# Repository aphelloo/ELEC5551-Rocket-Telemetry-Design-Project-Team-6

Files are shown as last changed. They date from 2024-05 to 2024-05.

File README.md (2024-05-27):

# ELEC5551-Rocket-Telemetry-Design-Project-Team-6
The purpose of this final design report is to present a TTS design for the UWAAL sub-orbital launch project. The design primarily aims to track the rocket’s sub-orbital launch to 4 km altitude, monitor its descent, identify the landing location for recovery efforts whilst also collect data throughout the entire mission. This is achieved through the development of two modules: one fitting within the designated section of the CubeSat onboard the rocket (i.e. the payload module) that collects & transmits data, and a base station on the ground responsible for collecting information from the payload module and displaying location of the payload module on a user interface akin to Google Maps functionality. The final design will be composed of a hardware and software solution that will address the inclusions stated in this section.

## Authors
* Shraddha Domdala 
* Sharla Greyvenstein 
* Kate Miller 
* Ankona Pahari
* Anusree Rejukumar
* Thomas Robertson

## Repository Structure
* 3D CAD Design: For Base Station Box and Battery Holder (payload module)
* Code: Includes pseudocode and code-flow diagrams
* Construction and Risks: Documentation on construction procedures and risk assessments associated with the project.
* Libraries: Libraries required for KiCAD to open schematics and PCB Layout
* PCB Layout: PCB Layout for base station and payload module
* Schematics: Schematics for base station and payload module
* Simulations: Simulations to test various aspects of the project

## Required Applications
* KiCAD V6 or Later
* MATLAB 2024a

## Library Installation Guide
Under Libraries
Using the *.kicad_sym file:

* Extract the content of the downloaded *.zip file.
* In KiCad, go to Preferences.
* Click on Manage Symbol Libraries.
* On the Global Libraries tab, click on Browse Libraries (the small folder icon)
* Select the .kicad_sym file, then click Open.
* The library will appear, click OK.
* Click on Symbol Editor.
* Type on the filter search field, and navigate to the symbol you imported.
* Double-click over it to open the file.

Using the *.kicad_mod file:

* Extract the content of the downloaded *.zip file.
* In KiCad, go to Preferences.
* Click on Manage Footprint Libraries.
* On the Global Libraries tab, click on Browse Libraries (the small folder icon)
* Navigate to the Folder where the .kicad_mod file is located. Then click Select Folder. (Note: You will not normally see the .kicad_mod file on this step because
  you need to select the folder where it is located.)
* The library will appear, click OK.
* Click on Footprint Editor.
* Type on the filter search field, and navigate to the footprint you imported.
* Double-click over it to open the file.

## Simulation File Installation Guide 
Files are under simulations > spice simulations
* Extract the content of the downloaded *.zip file.
* Go to the voltage regulator and right click on properties
* Then click on Simulation Model
* Click folder near the file tab
* Go to location of LM1117_N_ADJ_TRANS.LIB or TPS7A0530P_TRANS.lib depending on the file (see name of component to see which is right) - do not change anything else in that tab
* Ensure pin assignments for symbol and model pin match each other in the Simulation Model
* Click Ok in Simulation Model
* Click Ok in Properties Tab

## Acknowledgements
Would like to acknowledge the stakeholders of this project for their assistance

## Licence
This project is licensed under the CERN-OHL-P-2.0 license

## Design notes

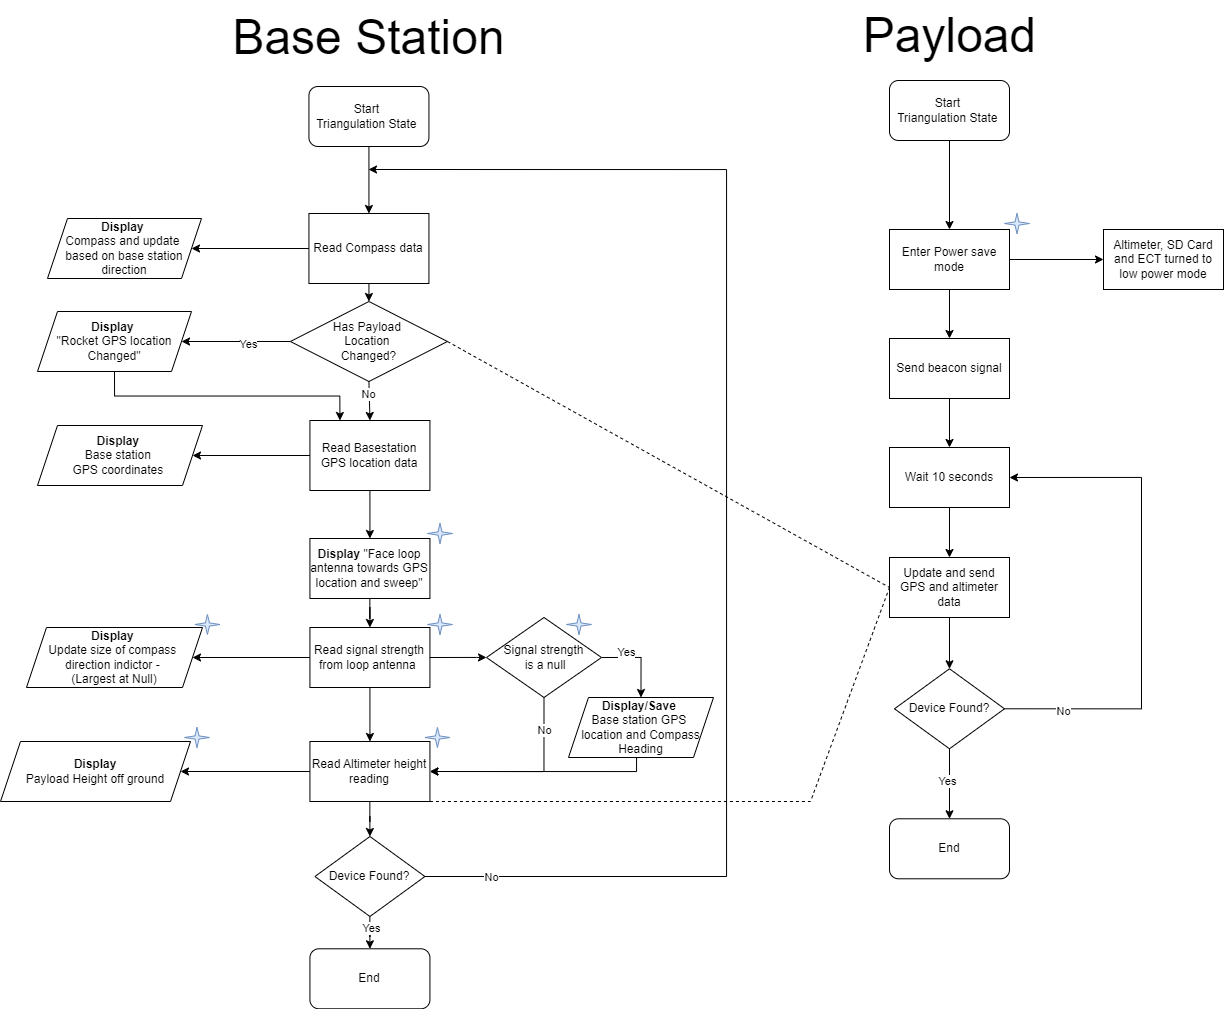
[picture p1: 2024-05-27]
Code/Code Flow/Triangulation Code Flow.png

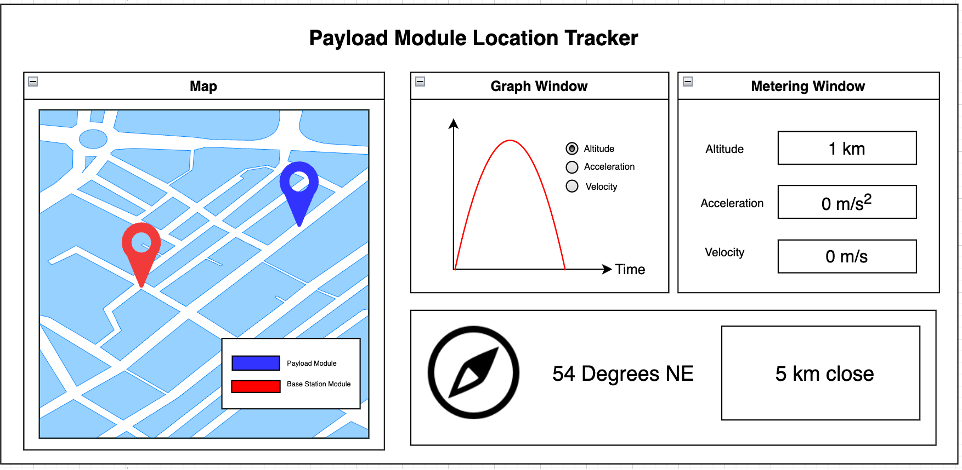
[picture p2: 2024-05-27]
Code/Pseudocode/User Interface Laptop.png

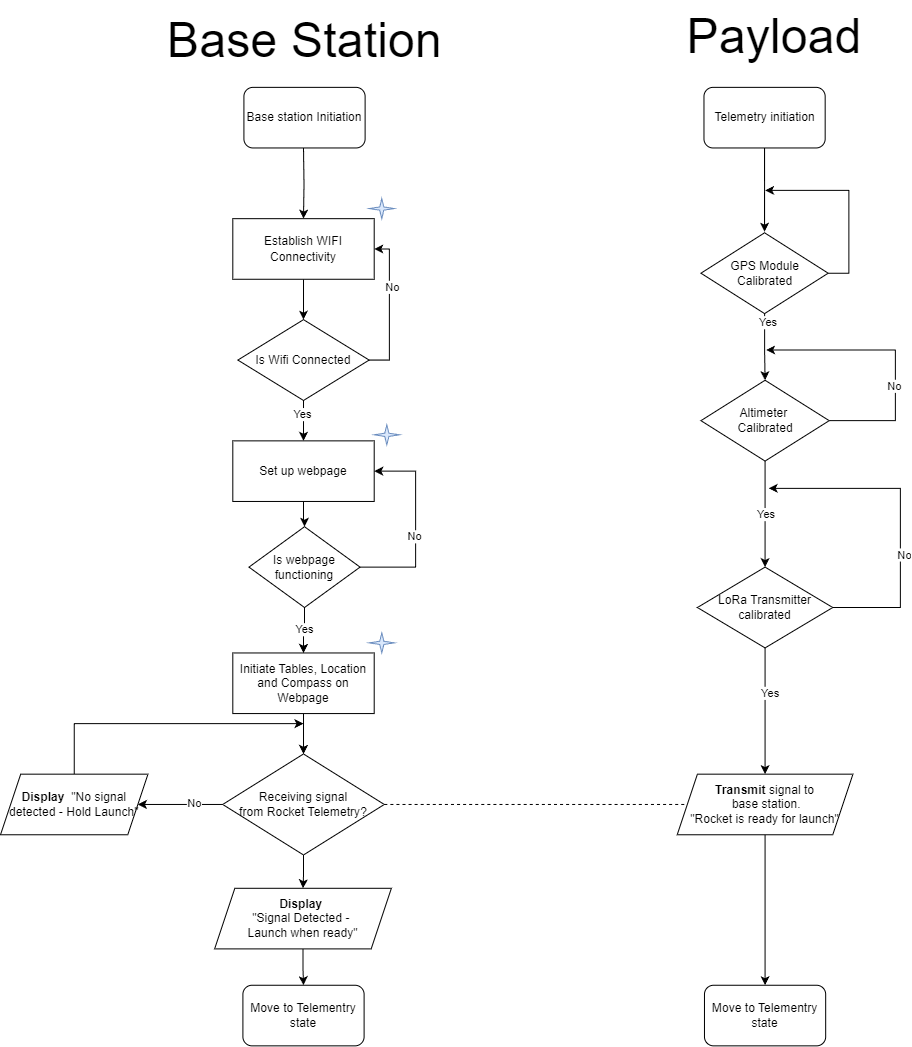
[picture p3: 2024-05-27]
Code/Code Flow/Initiation Code Flow.png

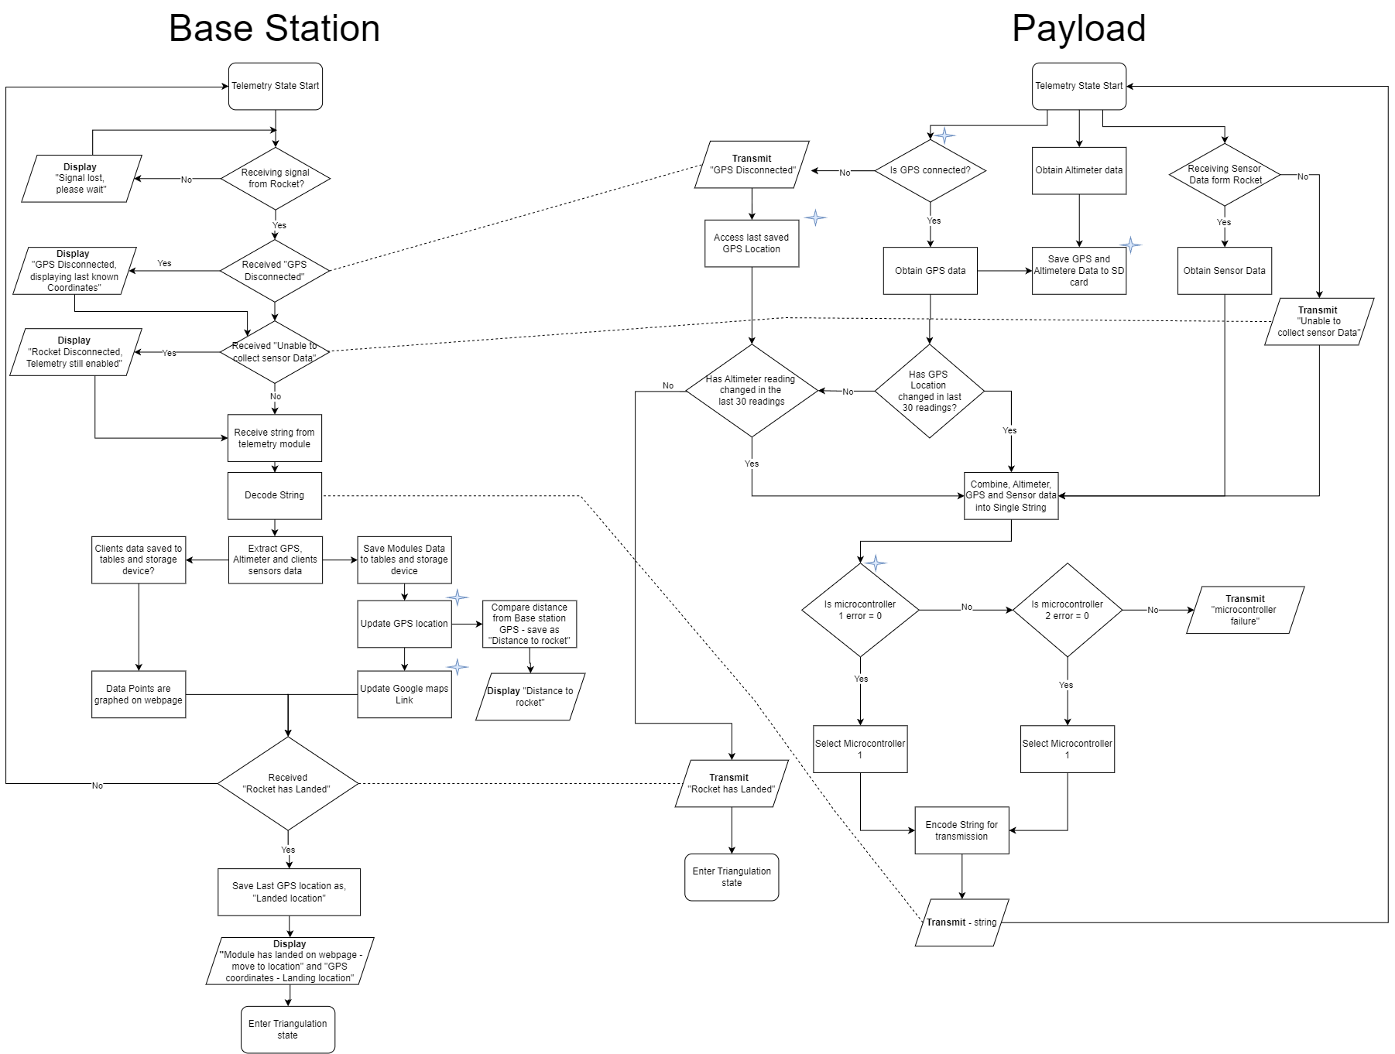
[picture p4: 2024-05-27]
Code/Code Flow/Telementry Code Flow.png

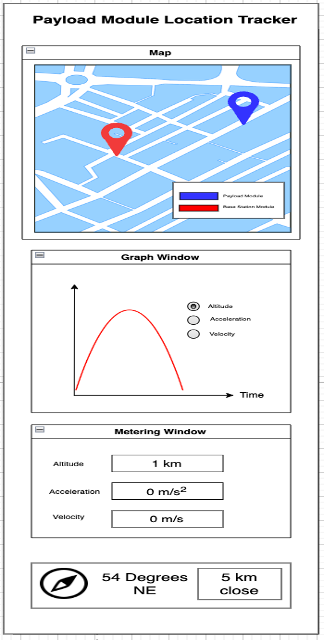
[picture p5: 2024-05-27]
Code/Pseudocode/User Interface Phone.png

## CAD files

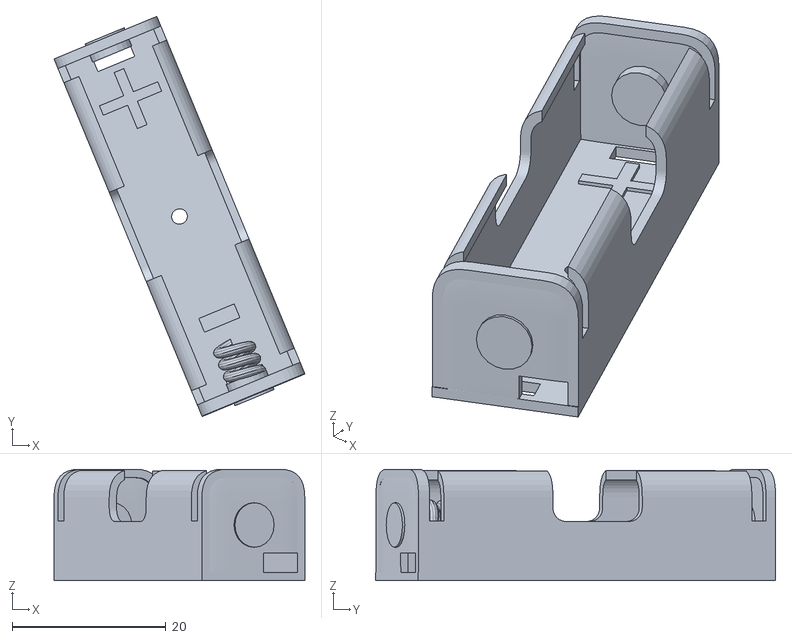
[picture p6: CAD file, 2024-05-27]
3D CAD Design/Team 6 Complete Battery Holder with Contacts and Springs.stl
32.7 x 52.1 x 14.5

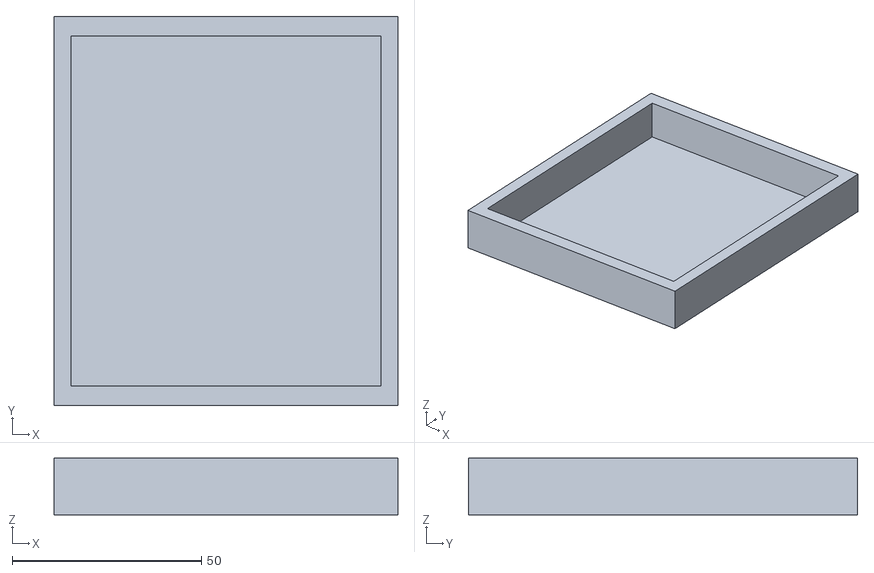
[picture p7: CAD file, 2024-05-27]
3D CAD Design/Team 6 Base Station Bottom.stl
91.0 x 103.0 x 15.0

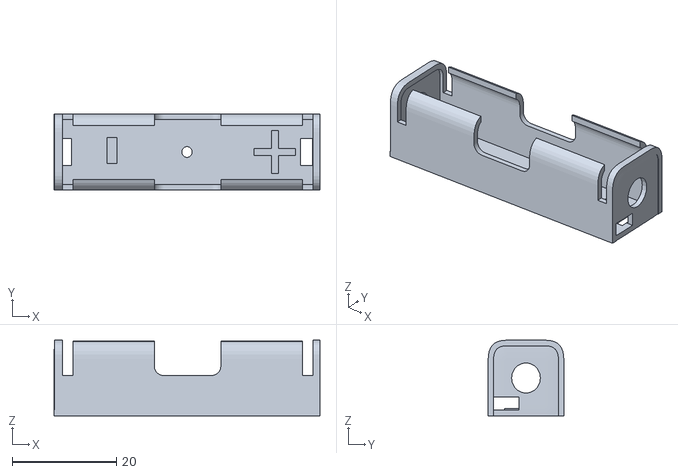
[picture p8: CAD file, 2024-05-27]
3D CAD Design/Team 6 Battery Holder without Contacts.stl
51.0 x 14.5 x 14.5

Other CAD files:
3D CAD Design/Team 6 Base Station Top.stl

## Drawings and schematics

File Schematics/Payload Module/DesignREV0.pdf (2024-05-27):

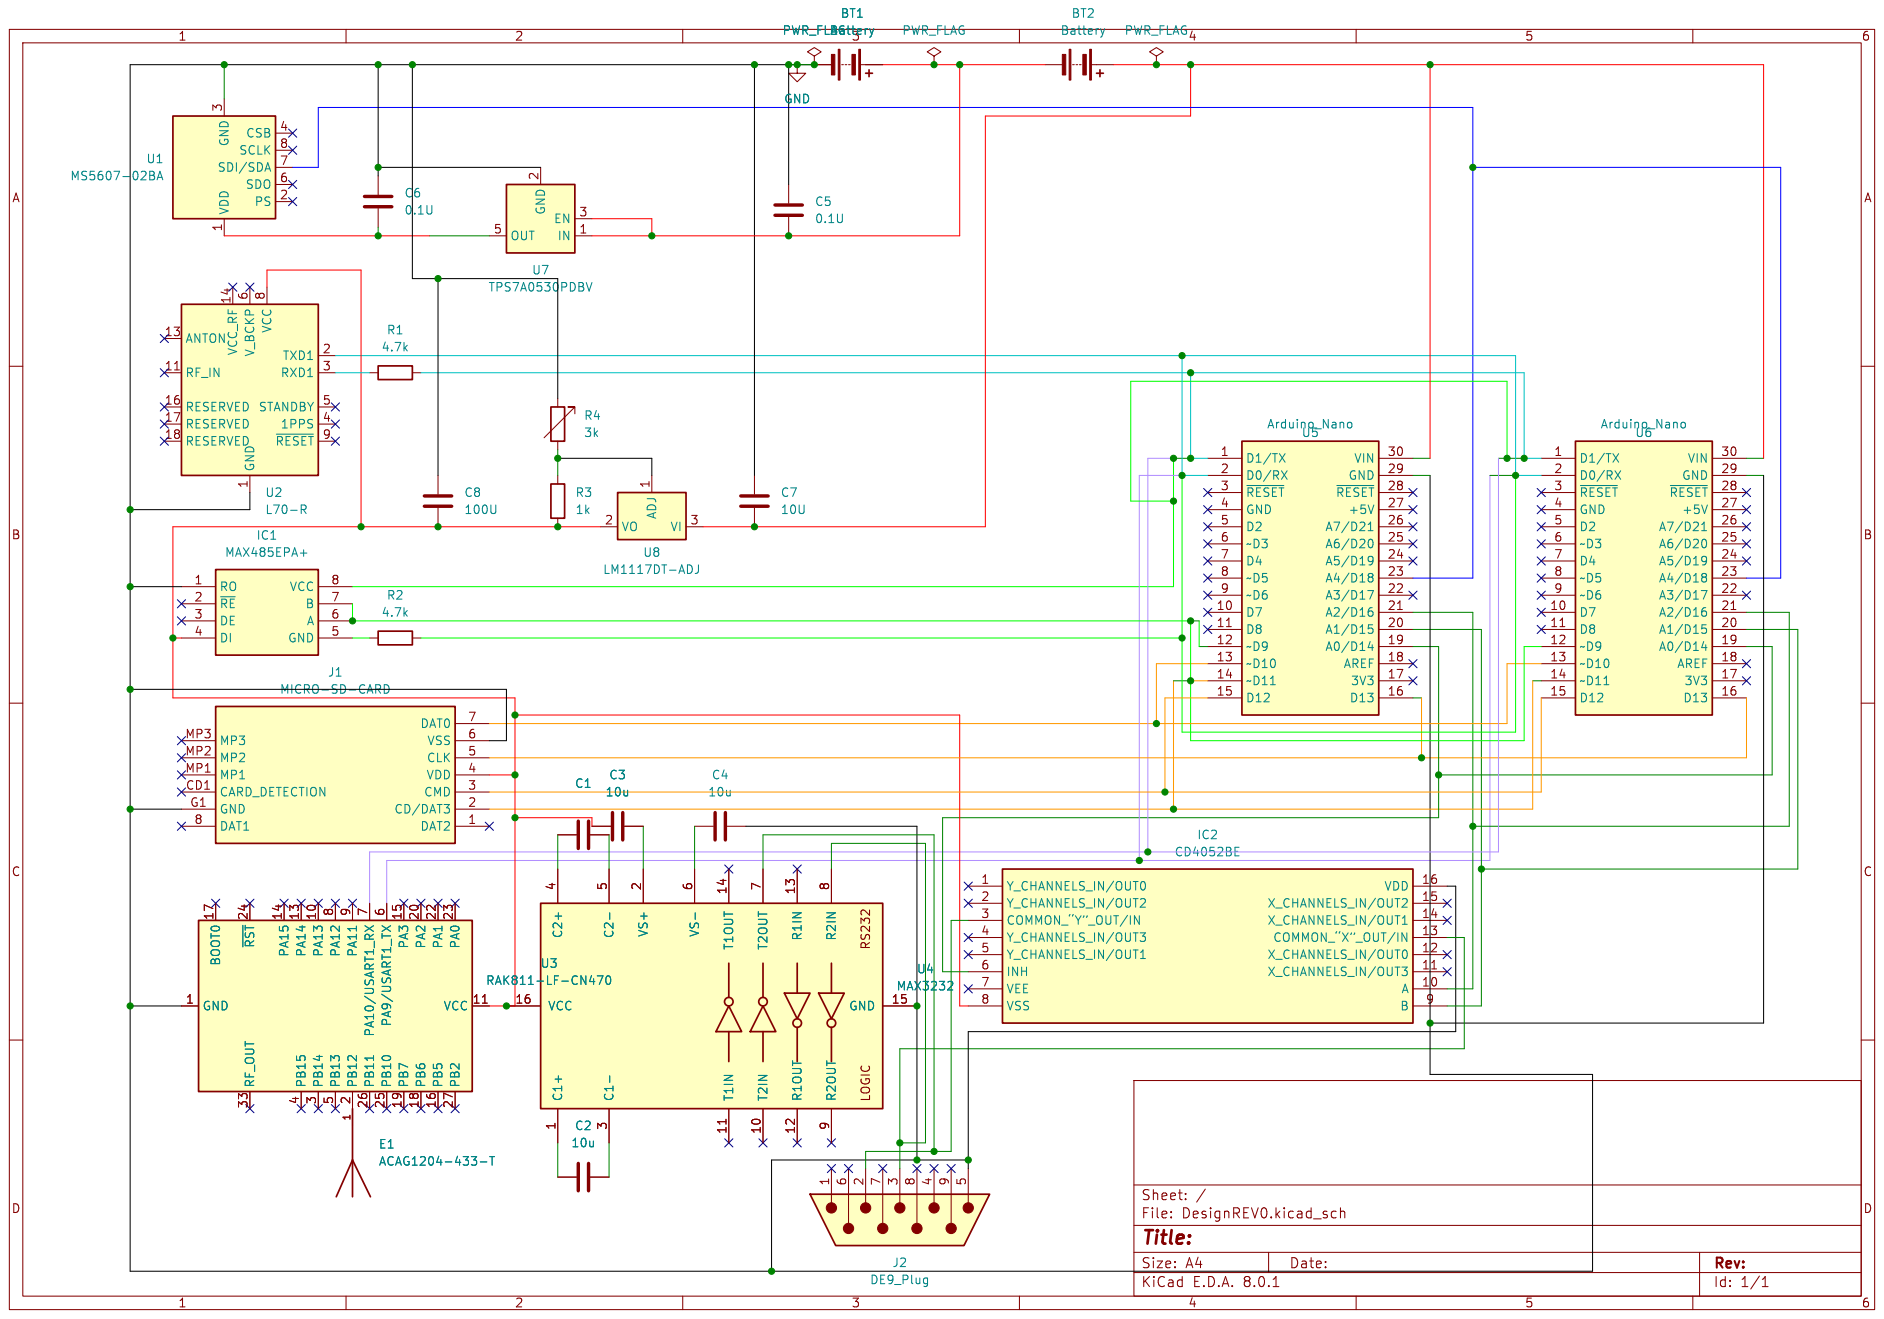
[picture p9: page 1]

3 CSB 4 SDO 6 SDI/SDA 7 SCLK 8 U1 MS5607-02BA

1 RF_IN 11 ANTON 13 VCC_RF 14 RESERVED 16 RESERVED 17 RESERVED 18 TXD1 2 RXD1 3

Id: 1/1 Title: File: DesignREV0.kicad_sch Sheet: /

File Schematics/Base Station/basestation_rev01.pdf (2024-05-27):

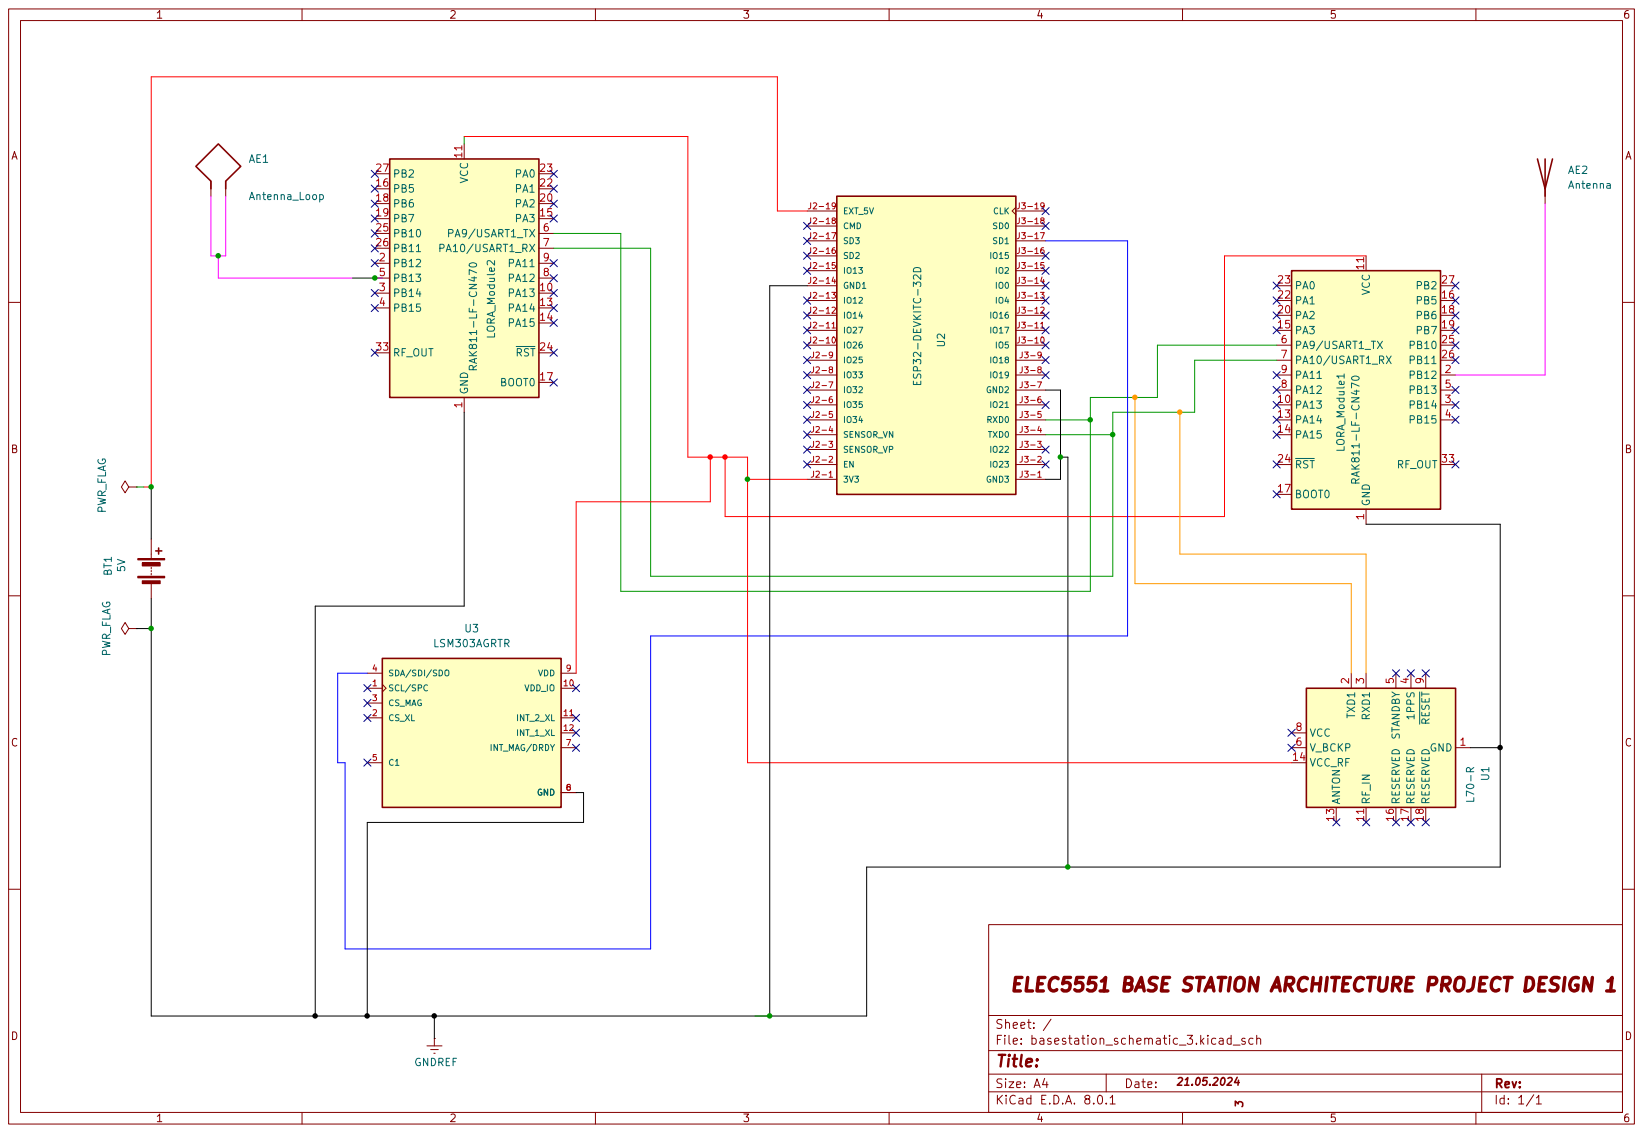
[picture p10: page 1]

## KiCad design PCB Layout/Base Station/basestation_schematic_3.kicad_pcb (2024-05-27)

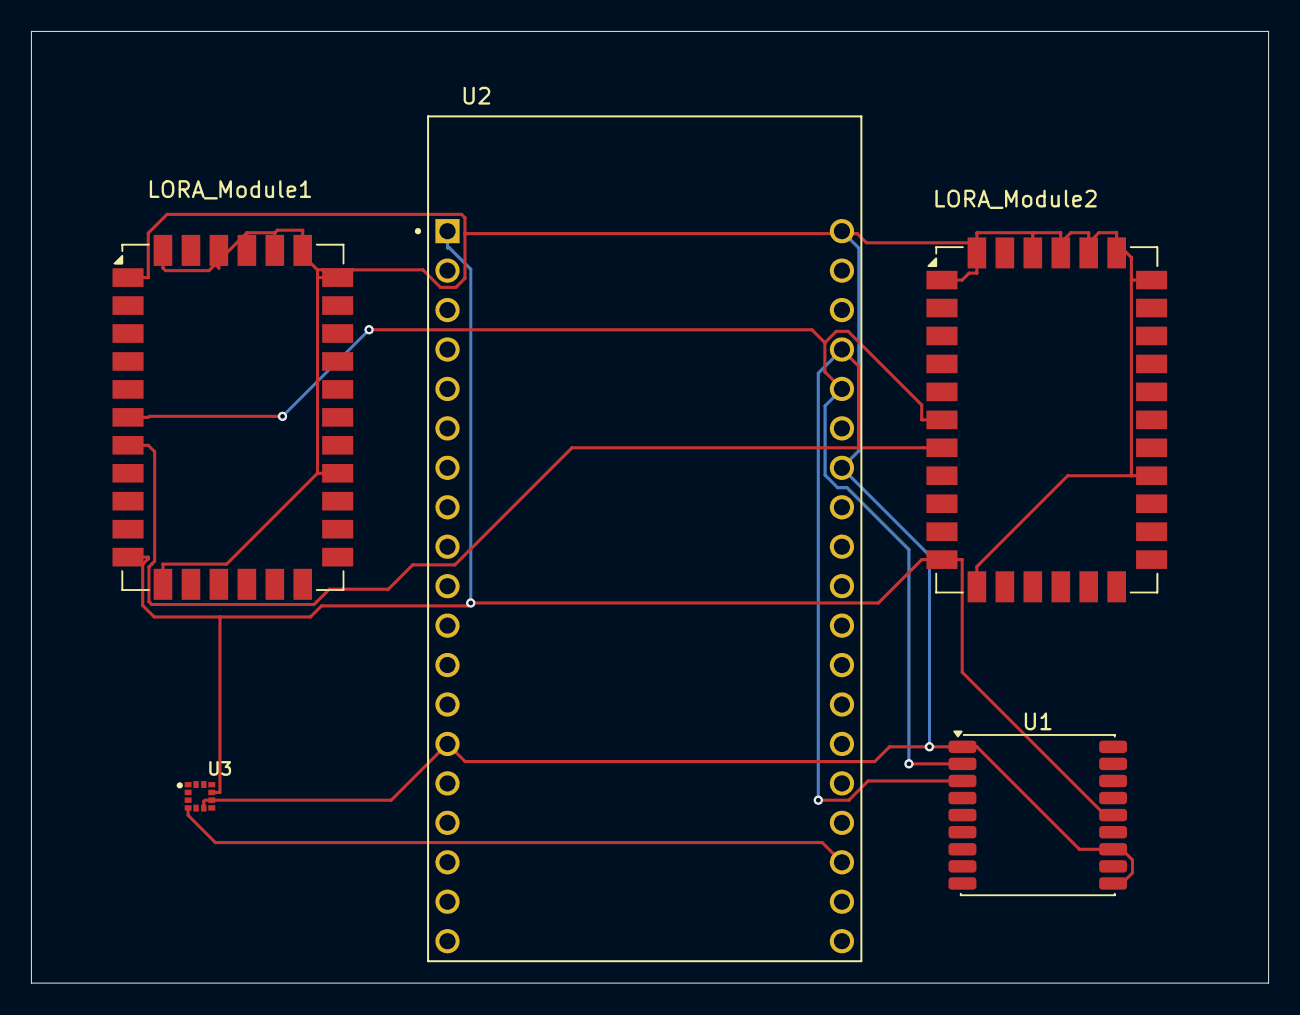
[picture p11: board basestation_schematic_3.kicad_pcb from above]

Board: 2 copper layers, 79.7 x 61.3 mm, 5 parts (0 on the bottom side), 5 nets.

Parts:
LORA_Module1, LORA_Module2: RAK811-LF-CN470; RAK811
U1: L70-R; Quectel_L70-R
U2: ESP32-DEVKITC-32D; MODULE_ESP32-DEVKITC-32D
U3: LSM303AGRTR; LGA12R50P_200X200X100

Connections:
GNDREF: LORA_Module1.1 (GND), LORA_Module1.12 (GND), LORA_Module1.21 (GND), LORA_Module1.28 (GND), LORA_Module1.29 (GND), LORA_Module1.30 (GND), LORA_Module1.31 (GND), LORA_Module1.32 (GND), LORA_Module1.34 (GND), LORA_Module2.1 (GND), LORA_Module2.12 (GND), LORA_Module2.21 (GND), LORA_Module2.28 (GND), LORA_Module2.29 (GND), LORA_Module2.30 (GND), LORA_Module2.31 (GND), LORA_Module2.32 (GND), LORA_Module2.34 (GND), U1.1 (GND), U1.10 (GND), U1.12 (GND), U2.J2-14 (GND1), U2.J3-1 (GND3), U2.J3-7 (GND2), U3.6 (GND), U3.8 (GND)
unnamed: LORA_Module1.6 (PA9/USART1_TX), LORA_Module2.6 (PA9/USART1_TX), U1.2 (TXD1), U2.J3-5 (RXD0)
unnamed: LORA_Module1.7 (PA10/USART1_RX), LORA_Module2.7 (PA10/USART1_RX), U1.3 (RXD1), U2.J3-4 (TXD0)
unnamed: LORA_Module1.11 (VCC), LORA_Module2.11 (VCC), U1.14 (VCC_RF), U2.J2-1 (3V3), U3.9 (VDD)
unnamed: U2.J3-17 (SD1), U3.4 (SDA/SDI/SDO)

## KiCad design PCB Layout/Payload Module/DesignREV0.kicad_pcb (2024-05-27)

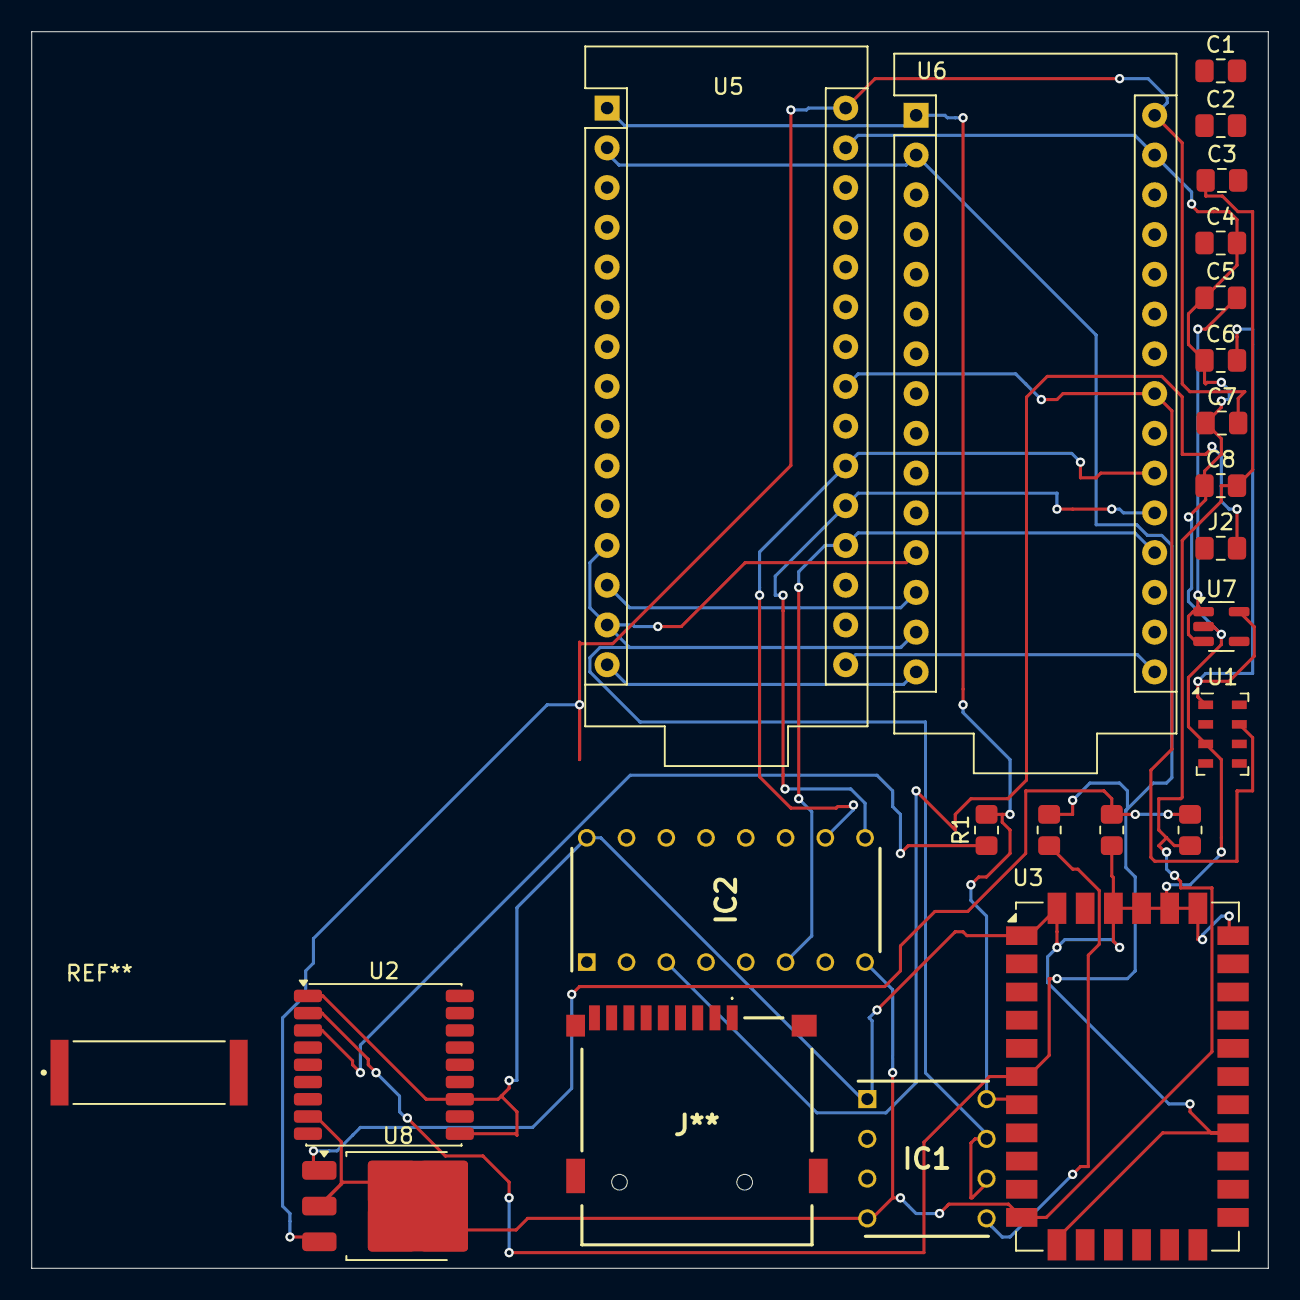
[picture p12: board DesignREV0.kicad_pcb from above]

Board: 2 copper layers, 79.0 x 79.0 mm, 23 parts (0 on the bottom side), 19 nets.

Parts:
C1, C2, C3, C4: 10u; C_0805_2012Metric_Pad1.18x1.45mm_HandSolder
C5, C6: 0.1U; C_0805_2012Metric_Pad1.18x1.45mm_HandSolder
C7: 10U; C_0805_2012Metric_Pad1.18x1.45mm_HandSolder
C8: 100U; C_0805_2012Metric_Pad1.18x1.45mm_HandSolder
IC1: MAX485EPA+; DIP762W56P254L938H457Q8N
IC2: CD4052BE; DIP794W53P254L1930H508Q16N
J2: DE9_Plug; C_0805_2012Metric_Pad1.18x1.45mm_HandSolder
J**: MICROSDCARD
R1, R2: 4.7k; R_0805_2012Metric_Pad1.20x1.40mm_HandSolder
R3: 1k; R_0805_2012Metric_Pad1.20x1.40mm_HandSolder
R4: 3k; R_0805_2012Metric_Pad1.20x1.40mm_HandSolder
U1: MS5607-02BA; LGA-8_3x5mm_P1.25mm
U2: L70-R; Quectel_L70-R
U3: RAK811-LF-CN470; RAK811
U5, U6: Arduino_Nano
U7: TPS7A0530PDBV; SOT-23-5
U8: LM1117DT-ADJ; TO-252-3_TabPin2

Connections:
GND: C4.2, C5.1, C6.1, C7.1, C8.1, IC1.1 (RO), IC2.16 (VDD), R4.1, U1.3 (GND), U2.1 (GND), U2.10 (GND), U2.12 (GND), U3.1 (GND), U3.12 (GND), U3.21 (GND), U3.28 (GND), U3.29 (GND), U3.30 (GND), U3.31 (GND), U3.32 (GND), U3.34 (GND), U5.29 (GND), U6.29 (GND), U7.2 (GND)
unnamed: C5.2, U7.1 (IN), U7.3 (EN)
unnamed: C7.2, U5.30 (VIN), U6.30 (VIN), U8.3 (VI)
unnamed: IC1.6 (A), IC1.7 (B), U5.12 (~D9), U5.14 (~D11), U6.12 (~D9), U6.14 (~D11)
unnamed: C3.1, C8.2, IC1.4 (DI), IC2.8 (VSS), R3.1, U2.8 (VCC), U3.11 (VCC), U8.2 (VO)
unnamed: IC1.5 (GND), R2.1
unnamed: IC1.8 (VCC), R1.2, U3.7 (PA10/USART1_RX), U5.1 (D1/TX), U6.1 (D1/TX)
unnamed: IC2.10 (A), U5.21 (A2/D16), U6.21 (A2/D16)
unnamed: IC2.9 (B), U5.20 (A1/D15), U6.20 (A1/D15)
unnamed: IC2.3 (COMMON_“Y”_OUT/IN), J2.2
unnamed: IC2.6 (INH), U5.19 (A0/D14), U6.19 (A0/D14)
unnamed: U5.16 (D13), U6.16 (D13)
unnamed: U5.15 (D12), U6.15 (D12)
unnamed: U5.13 (~D10), U6.13 (~D10)
unnamed: U1.7 (SDI/SDA), U5.23 (A4/D18), U6.23 (A4/D18)
unnamed: C6.2, U1.1 (VDD), U7.5 (OUT)
unnamed: R1.1, U2.3 (RXD1)
unnamed: R2.2, U2.2 (TXD1), U3.6 (PA9/USART1_TX), U5.2 (D0/RX), U6.2 (D0/RX)
unnamed: R3.2, R4.2, U8.1 (ADJ)

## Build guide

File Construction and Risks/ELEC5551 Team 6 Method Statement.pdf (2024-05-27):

Method Statement Title | Published: Month 2011 | Version 0.0
Authorised by: | Review: Month 2016 | Page 1 of 1
UNCONTROLLED WHEN PRINTED

# METHOD STATEMENT

LOCATION: | UWA Makers Lab
TASK/ACTIVITY: | Tracking Telemetry System
PREPARED BY | PERMISSION FOR TASK/ACTIVITY TO PROCEED
Name: | Team 6 | Name: | Michele
| | Signature:
Date: | 07/05/2024 | Date:

TICK
This document is part of a Job Safety Analysis (JSA) and reflects the findings of an associated risk assessment which is attached.

OR
JSA Waiver - There are no identifiable hazards associated with this activity which warrant further risk assessment or description.

Purpose
The purpose of this document is to outline the steps to building a rocket telemetry system (comprising of a base station and payload module), where the payload module fits within the allocated dimensions of the CubeSat (80mm x 80mm x 20mm) and is under 100g. The document includes both the hardware and software aspects of the design.

Scope
The design process systematically develops both hardware and software components necessary for transmitting and collecting telemetry data from CubeSat sensors, GPS modules, and altimeters.
Inclusions
- Programming the microcontrollers on both modules
- Configuring the antenna and transceivers (transmitter and receiver) for communication
- Soldering of components on PCB board
- Battery mounting
- Coating the PCB board with conformal resin
- Attaching the antennas to the transceivers
- Securing PCB within CubeSat
- Creation of a container for a base station (for safety of the components)
- Building the loop antenna
- Iterative testing to validate design and make any necessary changes. This comprises of looking at the effectiveness of the hardware (set-up and configuration) and software (Arduino program)
Exclusions
- Etching and drilling of the PCB board (will be externally procured)
- Container for the rocket PCB
- Alterations to the CubeSat
- Waterproofing of the module

Related Information
First the PCB boards and components must be procured. The transceivers will be configured to be able to communicate with one another using a temporary breadboard to connect them to a Serial USB Adapter which is inserted into a PC. The microcontrollers will also be inserted into a PC to be programmed. The components will then be soldered in their allocated positions and the PCB will be coated in resin. The battery holder and antennas will then be attached and the fully charged battery shall be placed in the holder. Some functional testings can be conducted in the lab to ensure that the GPS and altitude data is being transmitted and received and that information is accurate. The rocket PCB will then be secured within the allocated CubeSat space and the cable for CubeSat sensor data will be inserted into the communication port. The loop antenna being used for triangulation is then be created using a RG8 Coaxial. The steps for creating the loop antenna are as follows:
1) Use a tool to remove the outer protective sheet, 2) Peel back the copper braid, 3) Remove the centre core insulation and soldering, 4) Connect the two ends of the coaxial cable to a PL 259 Plug then a T piece allowing for the antenna to be connected to one of the LORA transceivers in the base station via coaxial cable. Finally, a container for the base station PCB will be created using a 3D printer, keeping the port to the Webserver open and LORA transceivers open. Edges may need to be trimmed and tidied.

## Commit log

2024-05-18 Create README for Schematics
2024-05-18 Create README for PCB Layout
2024-05-18 Create README for Battery Lifetime
2024-05-18 Create README for Code Flow
2024-05-26 Create 3D CAD Design Folder
2024-05-26 Battery Design Documentation
    The battery design documentation for telemetry or tracking of a rocket payload includes numerous critical sections to guarantee that all components of the project are fully covered. The introduction 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
2024-05-26 Update Battery Design Documentation
2024-05-27 Add files via upload
    3D Print of Base Station Box and Battery Holder
    [Team 6 Base Station Bottom.stl, Team 6 Base Station Top.stl, Team 6 Battery Holder without Contacts.stl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]
2024-05-27 Code Flow Addition
2024-05-27 Create Power Management Code
2024-05-27 Update Power Management
